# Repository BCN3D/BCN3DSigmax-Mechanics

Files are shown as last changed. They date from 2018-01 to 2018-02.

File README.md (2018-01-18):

## What’s hold in this repository?
This repository will hold all the information about the Mechanics of the BCN3D Sigmax.
As a declared Open Source organization, it's in our mission to release all the original design files to you to be able to learn, reuse and improve. Open Source not only means code, it also concerns hardware.

We’ve managed to design and manufacture the BCN3D Sigmax thanks to our previous experience in the 3D printing industry, the ideas coming from the community, our engineering background and a narrow collaboration with our suppliers. Our goal is justify the decisions we took and share the know-how we acquired so far.

We also provide the source files for those who want to check the core of the BCN3D Sigmax. You can consult both the CAD files and the technical drawings.

For a detailed explanation about the main pillars of the mechanical design of the Sigma and Sigmax, please check the repository [BCN3D Sigma - Mechanics](https://github.com/BCN3D/BCN3DSigma-Mechanics).

Regarding the Sigmax, the main objectives were:

 - Sigma and Sigmax must share as many references as possible

 - The Sigmax is targeting a more demanding customer, hence its performance and reliability must excel. 

The first goal was accomplished with a careful mechanical design, which ultimately allowed us to just modify few parts in the X and Z axis, change some wiring references and widen the aluminium frame. 

However, such big sheet metal parts, especially the frame, can be a challenge. Luckily, our previous experience in sheet metal manufacturing technologies eased the design process and the communication with our partners, so the suppliers have been able to provide high quality components since the very beginning of the production. 

The second goal has been achieved by improving the performance of certain key subassemblies. The most important change can be seen in the extruders. The Sigmax features the globally renowned Bondtech drivegears. These exceptional pieces of hardware, together with mighty stepper motors with planetary  gearbox has increased dramatically the reliability of the printer.

In addition, the Sigmax can be covered, a key feature for those intending to print large models with technical materials which may tend to warp. In order to ensure the safe operation of the printer, some heatsinks have been added in the most critical stepper motors.

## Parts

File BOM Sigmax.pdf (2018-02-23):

MANUFACTURER | CODE | PART NAME | UNITS
RiT | 14054 | A3BCN3DSigma Structure | 1
RiT | 14056 | Lower platform Sigma X | 1
RiT | 14057 | Reinforcement. Sigma X | 1
GLAS FORM S.L. | 14061 | Electronics cover Sigma X | 1
GLAS FORM S.L. | 14062 | Bottom cover Sigma X | 1
REMS | 14063 | ESPUMA TOP CC NEGRE FRESADO 750*550*85 Sigma X | 1
REMS | 14064 | ESPUMA CABEZALES CC BLANCO TROQ. 630 Sigma X | 1
MECANIZADOS CHAVES S.C.P. | 14065 | Transmission Bar Sigma X 675mm | 1
IGUS | 14073 | Cojinete de pedestal igubal®, Ø8mm KSTM-08 | 1
VIDRASA | 14066 | Placa borosilicato422x299x4mm | 1
ROBOTDIGG | 14067 | SSR25A DC-DC Solid-state Relay Sigma X | 1
ROBOTDIGG | 14045 | Motor heatsink black 28*28*15mm | 2
RUNICE | | GT2 OPEN BELT | 2
AXON' CABLE S.A.S. | 14052 | FFC Hotend 0 P567306A | 1
AXON' CABLE S.A.S. | 14053 | FFC Hotend 1 P567305A | 1
AXON' CABLE S.A.S. | 14051 | FFC Extruder 0 P567303A | 1
AXON' CABLE S.A.S. | 14050 | FFC X0 stepper P567304A | 1
CHANGZHOU SMART AUTOMATION | 14069 | Hot Bed Cable | 1
CHANGZHOU SMART AUTOMATION | 14070 | Power AC Cable | 1
CHANGZHOU SMART AUTOMATION | 14071 | Relay to mainboard Cable | 1
CHANGZHOU SMART AUTOMATION | 14072 | Power Supply to relay | 1
FLAK | 14075 | Caixa exterior cartró | 1
FLAK | | Caixa interior accesoris | 1
TAMEC | 14074 | Nozzel Offset Shim 0.05mm inox A.5 | 10
BONDTECH | 14044 | Drivegear kit 2,85/3,00 | 2
PRODUCTOS IMEDIO / bolton adhesives | 14077 | UHU STIC 21g | 1
MECANIZADOS CHAVES S.C.P. | 14049 | Extruder Body Left [X] | 1
MECANIZADOS CHAVES S.C.P. | 14048 | Extruder Tensor Left [X] | 1
MECANIZADOS CHAVES S.C.P. | 14047 | Extruder Body Right [X] | 1
MECANIZADOS CHAVES S.C.P. | 14046 | Extruder Tensor Right [X] | 1
RUNICE | 14068 | MGN9H rail 652mm Sigma X | 1
BARNES | 14082 | C0240-042-1000-M | 2
GRAMAGRAF | 14079 | Quick start guide Sigmax | 1
GRAMAGRAF | 11001 | Vinil logos | 1
ROBOTDIGG | | NEMA 17 40mm | 2
AIMAN G Z, S.L. | 10919 | Neodimio Aro 9.5-5.5-2 / NA009 | 4
KUONGSHUN ELECTRONIC | 10920 | Ball magnet 6mm diameter | 4
ALBIMAR | 10928 | Espátula 40mm / 18B305 | 1
ALBIMAR | 10934 | Tornavis estrella PH0X50 / 39D773 | 1
ALBIMAR | 10939 | Alicates 140mm C/Muelle / 32D726 | 1
ALBIMAR | 10964 | Llave Allen Pavonada 1,5mm | 1
ALBIMAR | 10965 | Llave Allen Pavonada 2,55mm | 1
ALBIMAR | 10966 | Llaven Allen Pavonada 4mm | 1
AXON' CABLE S.A.S. | 10858 | BCN3DSigma-Cable FFC X1 Motor | 1
AXON' CABLE S.A.S. | 10860 | BCN3DSigma-Cable FFC Z Motor | 1
AXON' CABLE S.A.S. | 10861 | BCN3DSigma-Cable FFC Y Motor | 1
AXON' CABLE S.A.S. | 10862 | BCN3DSigma-Cable FFC Extruder 1 | 1
BARNACORK S.L. | 10906 | Hotbed cork 297x210x3 mm corcho aglomerado | 2
REMS | 11037 | TOOL FOAM TRAY 310x210x35 scell R | 1
BRAFIM | 10976 | Conjunto protección Sigma protecció | 1
EET EUROPARTS | 10273 | Cable alimentación IEC 1,5m | 1

# BOM SIGMAX

MANUFACTURER | CODE | PART NAME | UNITS
EET EUROPARTS | 10082 | Cable USB 2.0 1,8m / CU03 | 1
CHANGZHOU SMART AUTOMATION | 10869 | BCN3DSigma-Cable LCD 0P12D | 1
CHANGZHOU SMART AUTOMATION | 10871 | BCN3DSigma-Cable Endstop Y | 1
CHANGZHOU SMART AUTOMATION | 10872 | BCN3DSigma-Cable Endstop X | 2
CHANGZHOU SMART AUTOMATION | 10873 | BCN3DSigma-Cable Endstop Z | 2
CHANGZHOU SMART AUTOMATION | 10874 | BCN3DSigma-Cable SD 0P19C | 1
CHANGZHOU SMART AUTOMATION | 10901 | SM35HT36-1004A-08A (Nema 14 36mm) | 2
CHANGZHOU SMART AUTOMATION | 10903 | SM42HT33-1334L with Tr8*2 260mm length + nut | 1
CHANGZHOU SMART AUTOMATION | 10987 | SM42HT47-1684A-37F (nema 17 42mm) | 1
ALBIMAR | 10992 | Arandelas nylon 3.2x7x0.5 | 38
ALBIMAR | 10826 | Patas para tornillo 7,1x15,9mm / 15129 | 4
ALBIMAR | 10931 | Nylon UL94 V2 6/6, RMS-01 / N-5E | 4
| 10828 | BCN3DSigma-Stepper Holder Right | 1
RiT | 10829 | BCN3DSigma-Stepper Holder Left | 1
RiT | 10830 | BCN3DSigma-X Axis Idler | 2
RiT | 10831 | BCN3DSigma-Belt Clamp | 2
RiT | 10835 | BCN3DSigma-Lower Cover | 2
RiT | 10836 | BCN3DSigma-Upper Cover | 2
RiT | 10837 | BCN3DSigma-Hotend Plate | 2
RiT | 10838 | BCN3DSigma-Y Axis Idler | 2
RiT | 10839 | BCN3DSigma-Y Idler Tensioner | 2
RiT | 10840 | BCN3DSigma-Guide Spacer | 2
RiT | 10843 | BCN3DSigma-SD Holder | 1
RiT | 10845 | BCN3DSigma-Spool Support | 4
RiT | 10846 | BCN3DSigma-X Support | 2
RiT | 10847 | BCN3DSigma-Connection plate | 2
RiT | 10849 | BCN3DSigma-Purger Base Left | 1
RiT | 10850 | BCN3DSigma-Purger Base Right | 1
RiT | 10851 | BCN3DSigma-X Plate Left | 1
RiT | 10852 | BCN3DSigma-X Plate Right | 1
RiT | 10853 | BCN3DSigma-Connection Board Support | 2
RiT | 10854 | BCN3DSigma-Y Stepper Holder | 1
RiT | 10918 | BCN3DSigma-Extruder driver cover | 2
RiT | 10956 | BCN3DSigma-X Stepper Driver Holder Left | 1
RiT | 10957 | BCN3DSigma-X Stepper Driver Holder Right | 1
RiT | 10983 | BCN3DSigma-Z Stepper Holder | 1
FERPLAST, S.L. | 10894 | BCN3DSigma-Window PET-G 2mm incoloro | 2
FLAK SL. | 11035 | tub eines | 1
GLAS FORM S.L. | 10890 | BCN3DSigma-Inner covers PS blau | 1
GLAS FORM S.L. | 10892 | BCN3DSigma-LCD cover PS blau | 1
GRAMAGRAF | 11001 | BCN3D Sigma Logo (2 logos) | 1
GRAMAGRAF | 11002 | SIGMA CE Label | 1
GRAMAGRAF | 11004 | Hot surface Label+ Warning hard injury | 2
GRAMAGRAF | 11006 | Adesivo Tuercas | 2
GRAMAGRAF | 10969 | FOLLETOS GARANTIA + quick start guide | 1
I.M.C. esquerda S.L. | 10915 | Silicone Cloth Pieza 36x13x2 mm silicona | 2
RUNICE | 10446 | Pulley GT2, 20 Teeth 5mm Bore for 6mm width belt | 2
RUNICE | 11071 | Idler pulley 20 teeth | 4
RUNICE | 10875 | MGN9H rail 360 mm | 2
JINAN YUKI | 10877 | LMF12UU Linear bearing | 2
JINAN YUKI | 10878 | SK12 Shaft Support | 4
RUNICE | 10879 | KFL08 Bearing Pillow Block | 2
RUNICE | 10883 | GT2 Pulley 20 teeth 8mm bore for 12mm width belt | 1

MANUFACTURER | CODE | PART NAME | UNITS
RUNICE | 10884 | GT2 Pulley 20 teeth 5mm bore for 12mm width belt | 1
RUNICE | 10885 | GT2 Pulley 20 teeth 8mm bore for 6mm width belt | 2
JINAN YUKI | 10886 | Ball Bearing MR105zz | 2
RUNICE | 10880 | GT2 Belt 6mm width closed belt 810mm | 2
RUNICE | 10882 | GT2 Belt 12mm width closed belt 112mm | 1
KUONGSHUN ELECTRONIC | 10897 | PTFE Teflon Tube, ID=4mm OD=6mm [m] / Q99 | 1
ULIKELED | 10945 | Led strip RGB 5050 assembled | 2
ARES | 10973 | SD Reader | 1
KUONGSHUN ELECTRONIC | 10476 | USB Cable Extension | 1
MECANIZADOS CHAVES S.C.P. | 10899 | BCN3DSigma-Y Belt tensor | 1
MECANIZADOS CHAVES S.C.P. | 10900 | BCN3DSigma-Hot block HE | 2
MECANIZADOS CHAVES S.C.P. | 10905 | BCN3D Sigma-Z Bar | 2
MECANIZADOS CHAVES S.C.P. | 10911 | BCN3DSigma-Heatbreak HE | 2
MECANIZADOS CHAVES S.C.P. | 10912 | BCN3DSigma-Heatsink HE | 2
MECANIZADOS CHAVES S.C.P. | 10986 | Idler Pulley Shaft | 4
MISCO | 10210 | SD Card 8GB | 2
MUELLES Y RESORTES BOSCH, S.L. | 10895 | Muelle 15,75xINT=5,7x1:E7 AMOLADO / M03C02.0P04Z | 3
MUELLES Y RESORTES BOSCH, S.L. | 10896 | Muelle 25,4xINT=3,96X1,1:E:14,5 AMOLADO / M07C00.0P13Z 2
ONDARADIO | 10887 | Power Supply 24V 320W / RSP-320-24 | 2
AXON' CABLE S.A.S. | 10982 | TUBE PTFE 3.18x6.35mm Natural | 2,1
DECOLETAJE 9002 | 10922 | Pneufit Coupling | 6
DECOLETAJE 9002 | 10923 | NOZZLE 0,4mm SIGMA | 2
RIERA I TUTÓ | 10841 | BCN3DSigma-Square 90 | 8
RIERA I TUTÓ | 10842 | BCN3DSigma-Square 60 | 2
RS AMIDATA | 11060 | Pantalla uLCD-35DT 4D Systems (125-7946) | 1
RS AMIDATA | 10924 | Coupling collet unión 1/4" / PI0408S (896-8333) | 14
KUONGSHUN ELECTRONIC | 10926 | SS-5-FD MICROSWITCH, 5A, PIN, SPDT, SOLDER / 682-2657 | 5
ALBIMAR | 10930 | Espaciador Redondo, Poliamida, negro 3,2x6x3 / 102-6110 | 14
RS AMIDATA | 10933 | Prensacables Adhesivos Planos / 233-190 | 11
RS AMIDATA | 10935 | Interruptor de balancín, 1881.1103 / 741-0912 | 1
RS AMIDATA | 10936 | Fusible 250V 10A 5x20mm / 541-4533 | 2
RS AMIDATA | 10938 | Cinta adhesiva Advance Tapes 205882 Blanco Mate [m] / 239-4600 1,8
RS AMIDATA | 10991 | Conector filtro IEC950 FN9260-2-06 / 188-9618 | 1
SHENZHEN XINYUJIE | 10916 | Axial fan 4010 24V 130mm PHR 2 / AV-F4020HB | 2
GICODA | 11034 | ventilador 3010 12V | 2
ARES | 11070 | Stepper Driver X axis | 2
ARES | 10907 | Stepper Driver YZE axis | 4
ARES | 10908 | Heated Bed | 2
ARES | 10909 | Mother Board | 1
ARES | 10910 | Extruder Board | 2
UTILNORM, S.L | 10888 | High Knurled Knut DIN 466 M5 / ULM 06110-05 | 2
UTILNORM, S.L | 10889 | Botón moleteado con rosca interior / 06094-004 | 4
YANCHENG XUANYUAN | 10977 | Subkit 21 (Cable Hotend) | 4
HIWIN BLOCK TECNOPOWER | 11094 | | 4

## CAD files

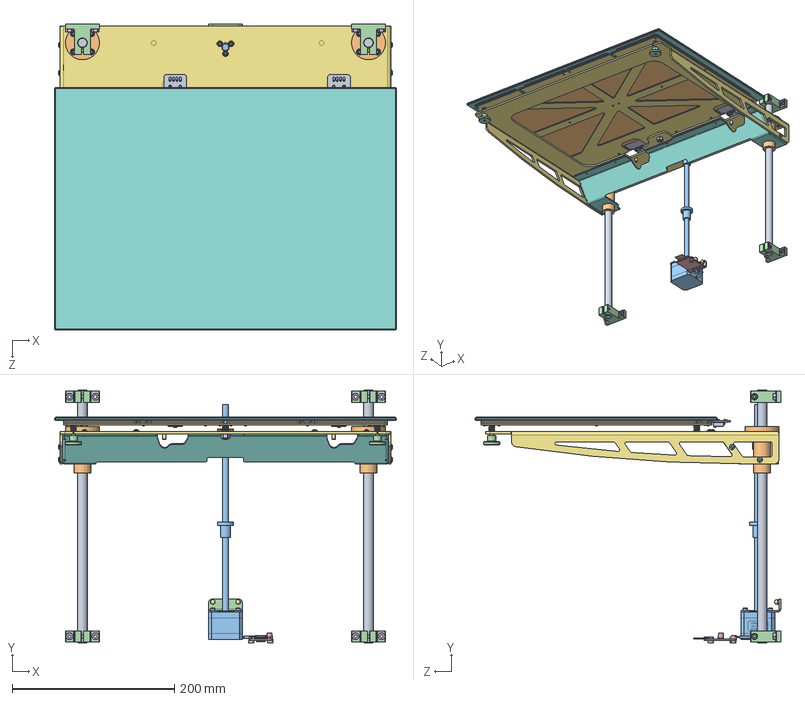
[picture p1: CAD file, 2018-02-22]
CAD/SLDPRT2016/040M03C00.0P000 Z axis.SLDASM
422.0 x 312.0 x 377.2 mm
A3DIN912 M3x6 x 8
A3DIN912 M3x8 x 3
A3DIN7981 3.2x6.5 x 9
A3DIN912 M4x12 x 4
A3DIN125 M3 x 12
A3DIN934 M5 x 8
040M03C01.0P01G Lower platform
040M03C01.0P02D Reinforcement
040M03C01.0P03B Z Bar x 2
040M03C01.0P04Z Flanged Linear Bushing x 2
040M03C01.0P05Z Z Nut
040M03C01.0P06Z Shaft Support x 4
A3DIN7991 M3x6 x 18
A3DIN985 M5
040M03C02.0P01D Upper platform
040M03C02.0P02B Glass
040M03C02.0P05E Heated bed x 2
040M03C02.0P03C Cork x 2
040M03C02.0P04Z Printing surface spring x 3
040M03C02.0P07Z Bed Thumbscrew x 2
040M03C02.0P09A Thumbscrew Label x 2
040M03C02.0P06Z Magnet x 4
A3DIN1587 M3 x 2
A3DIN912 M3x10 x 3
A3DIN934 M3 x 2
A3DIN125 M3 poliamida x 2
040M03C03.0P01Z Z Motor
040M03C03.0P02B Z Stepper Holder
040M04C00.0P03F Stepper Driver Board
040M04C00.0P06Z Ariston Spacer 3mm x 2

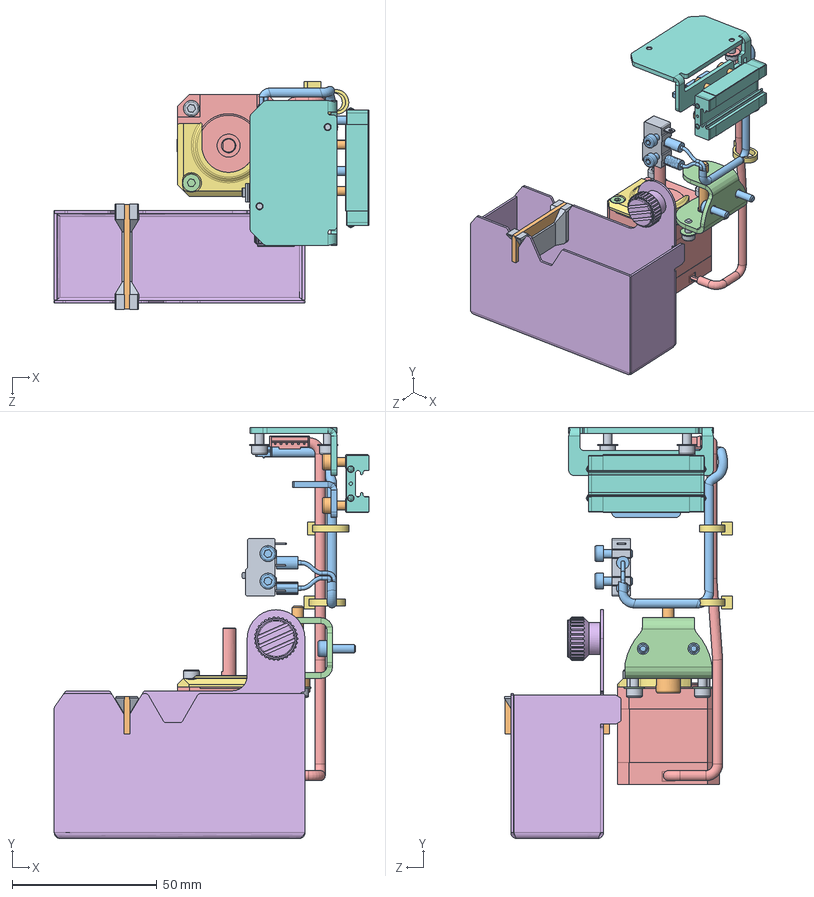
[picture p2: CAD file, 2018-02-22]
CAD/SLDPRT2016/040M05C02.0P000 X Axis Right.SLDASM
108.6 x 141.9 x 78.8 mm
A3DIN912 M3x6 x 7
A3DIN912 M3x8 x 4
A3DIN912 M3x10 x 4
A3DIN7991 M3x6
A3DIN125 M3 poliamida x 2
040M05C02.0P02C Purger Base Right
040M05C02.0P03B Stepper cover right
040M05C02.0P04B X Stepper Driver Holder Right
040M02C01.0P08Z Endstop
040M02C01.0P10A Idler pulley shaft
040M05C01.0P01D Belt Clamp
040M05C01.0P03E X Axis Idler
040M05C01.0P5Z Nema 14
040M05C01.0P08Z Purger Button
040M09C00.0P20A Zip tie x 2
040M05C00.0P02ALinear guide slide
040M05C01.0P14A Cloth Support
040M05C01.0P07A Silicone Cloth
040M09C00.0P15A Endstop X Right
A3DIN125 M3 x 2

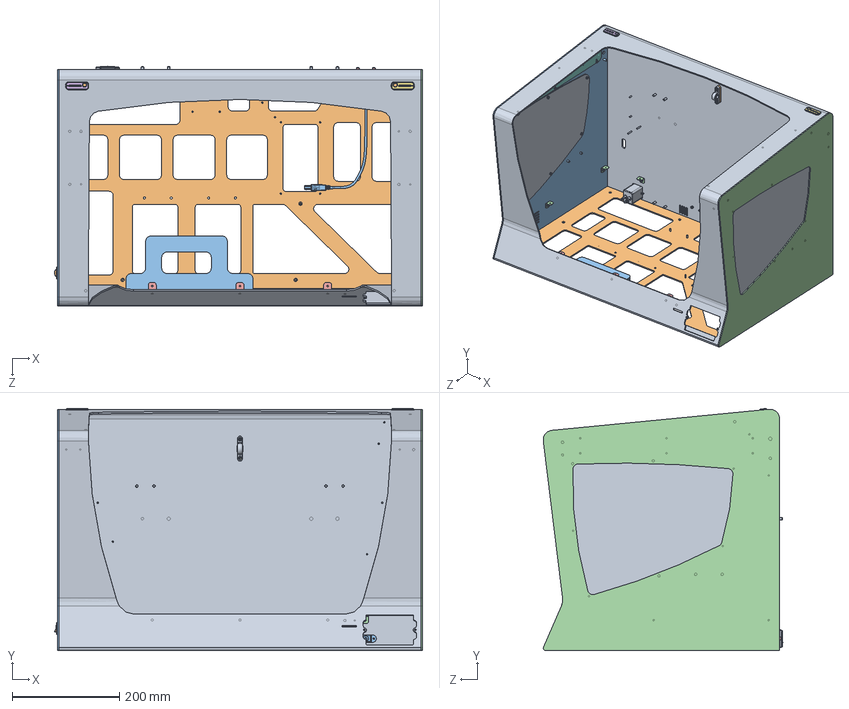
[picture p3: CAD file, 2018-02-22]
CAD/SLDPRT2016/040M01C01.0P000 Main Structure.SLDASM
686.9 x 451.8 x 447.2 mm
040M01C01.0P01G Top frame
040M01C01.0P02D Bottom frame
040M01C01.0P03C Left side
040M01C01.0P04C Right side
040M01C01.0P05C Y Idler Tensioner x 2
040M01C01.0P29F Bowden exit Left
040M01C01.0P29F Bowden exit Right
040M01C01.0P07F Guide spacer x 2
040M01C01.0P08B Window x 2
040M01C01.0P11Z Power button
040M01C01.0P12Z USB Extension Cable
040M01C01.0P15A Square 90 x 8
040M01C01.0P16A Square 60 x 3
040M01C01.0P30A Curve flat cable holder Right x 2
040M01C01.0P20C Front LED connector clamp x 2
040M01C01.0P22D Plain flat cable holder x 4
040M04C00.0P07Z Power Entry Filter
040M01C01.0P17Z Fusible
A3DIN913 M4x4 x 12
DIN7982 M3.5x13 x 2
A3DIN912 M3x10 x 2
A3DIN125 M3 poliamida x 14
A3DIN934 M3 x 48
A3DIN985 M3 x 9
040M02C01.0P14A DRY-RUNNING MOUNTED SLEEVE BRNG
040M02C01.0P15A Y Axis Pillow Bearing Spacer

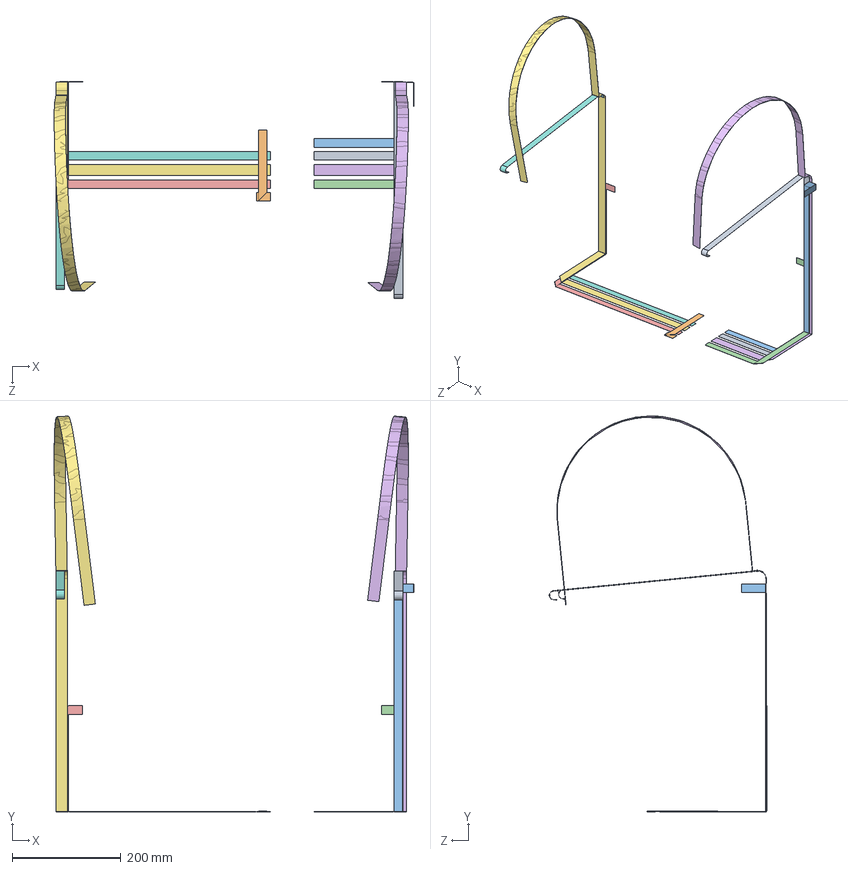
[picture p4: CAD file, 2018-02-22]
CAD/SLDPRT2016/040M09C00.0P000 Wiring.SLDASM
661.3 x 728.0 x 399.5 mm
040M09C00.0P01A FFC X1 stepper
040M09C00.0P03A FFC Z stepper
040M09C00.0P04A FFC Y stepper
040M09C00.0P05A FFC Extruder 1
040M09C00.0P06B FFC Extruder 0
040M09C00.0P08A FFC Hotend 1
040M09C00.0P07B FFC Hotend 0
040M09C00.0P02B FFC X0 stepper

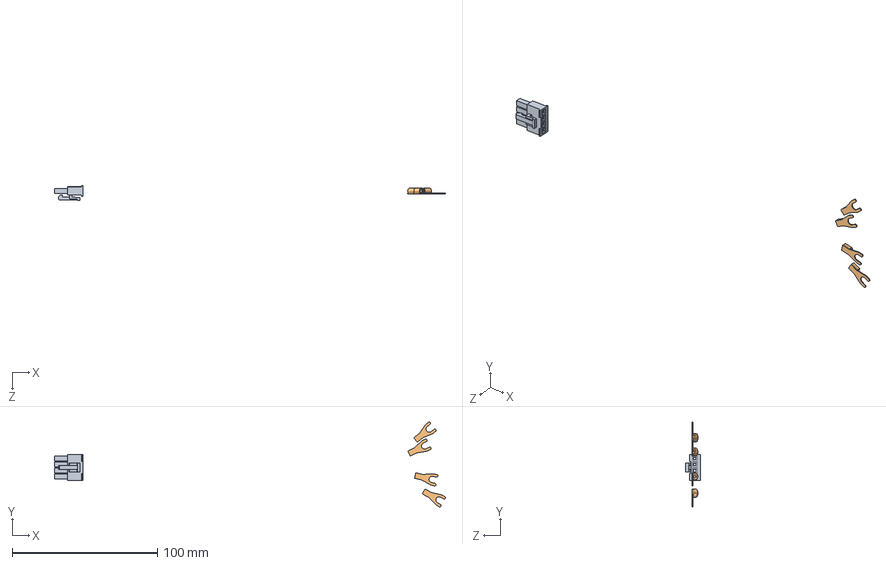
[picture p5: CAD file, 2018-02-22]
CAD/SLDPRT2016/040M09C00.0P11B Power DC cable.sldasm
268.9 x 58.3 x 10.2 mm
A3039014040
A3JST_GS42,5C x 4

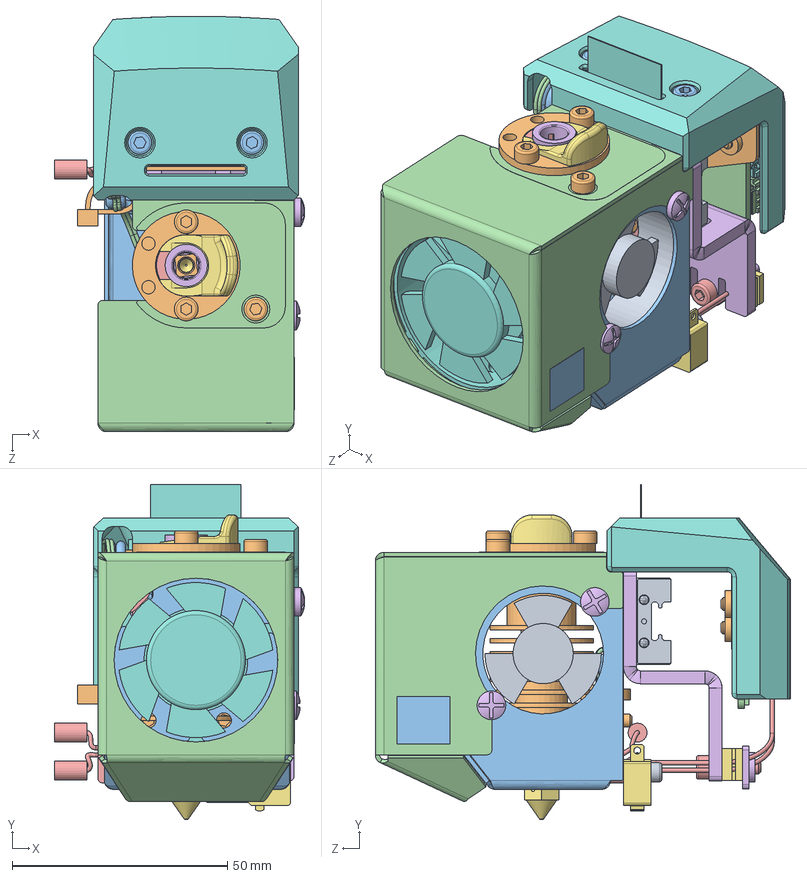
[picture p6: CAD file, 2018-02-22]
CAD/SLDPRT2016/040M06C01.0P000 Left Hotend.SLDASM
58.0 x 77.8 x 96.4 mm
A3DIN912 M2,5x10 x 2
A3DIN912 M3x6 x 9
A3DIN912 M3x8 x 4
A3DIN912 M3x18 x 3
A3DIN7991 M3x10 x 2
A3DIN7981 9.5x3.2_RationalStock x 2
A3DIN125 M3 poliamida x 4
040M06C01.0P01D Conexion cover
040M06C01.0P03Z Heat sink fan
040M06C01.0P04C Connection board support
040M06C01.0P05E Lower cover
040M06C01.0P06D Upper cover
040M06C01.0P07D Hotend Plate
040M06C01.0P08G X Plate Left
040M02C01.0P08Z Endstop
040M06C01.0P09Z Layer fan
040M06C01.0P11B Cable clip
040M06C01.0P12B Layer fan spacer
040M06C01.0P13A Flat cable clip
040M04C00.0P04B Hotend Board
040M09C00.0P16B Endstop Z Left
A3DIN913 M3x3 x 2
040M06C03.0P01C Nozzle 0.4
040M06C03.0P02C Heatbreak
040M06C03.0P03A Hot block
040M06C03.0P04G Heatsink bowden
040M06C03.1P01B Resistance 24V
040M06C03.1P02B Thermistor
040M07C01.0P04D Pneufit coupling
040M07C01.0P19Z Coupling collet
040M07C01.0P14B Coupling Clip
A3Connexio cable pla hotend
040M05C00.0P02ALinear guide slide
040M09C00.0P20A Zip tie
040M06C01.0P14A Hot surface Label
Nozzel Offset Shim 0.05mm A.5
A3DIN912 M3x12
HNKK5-3
GT2_clamp_0.1_offset - A.3

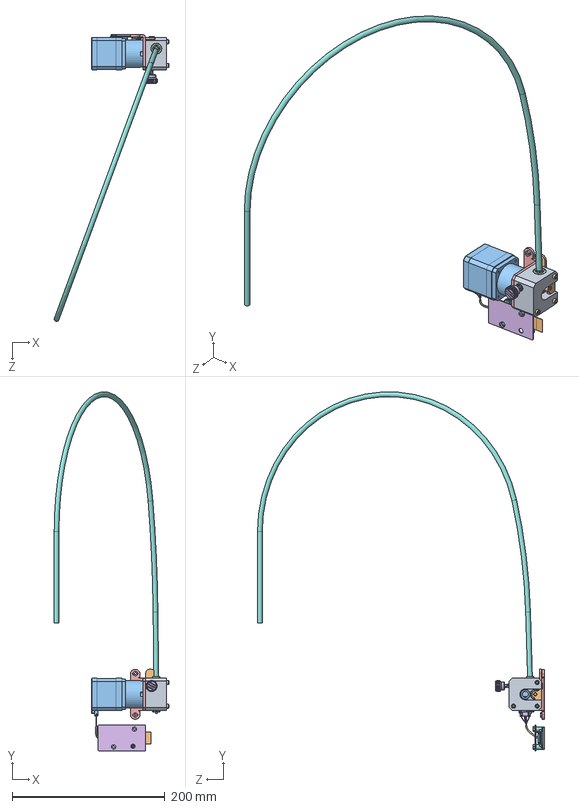
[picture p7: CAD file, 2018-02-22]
CAD/SLDPRT2016/040M07C02.0P000C Right extruder.SLDASM
150.2 x 470.4 x 376.1 mm
A3DIN934 M3 x 4
A3Connexio cable pla 15 vies
040M07C01.0P10AA Nema 17 40mm
040M07C01.0P04D Pneufit coupling x 2
040M07C01.0P05E Extruder Stepper Holder
040M07C01.0P06B Extruder driver cover
040M07C01.0P19Z Coupling collet x 2
040M04C00.0P03F Stepper Driver Board
040M07C02.0P026D Extruder Body Right
040M07C02.0P027B Extruder Tensor Right
040M07C01.0P25Z Driving Gear
040M07C01.0P24Z Driven Gear
Passador 4x24
040M05C01.0P08Z Purger Button
filament
Separador nylon negre 3.2x6x8 x 2
BCN3DSigma-M05C01.0P11C Driver spacer
A3DIN912 M3x30 x 3
040M07C01.0P13A Extruder spring
DIN931 M4x50 (91280A154)
A3DIN912 M3x8 x 3
PHR-6_PRUEBA x 2
Cable^040M07C01.0P01A Right extruder Cable
040M07C01.0P07B Bowden tube

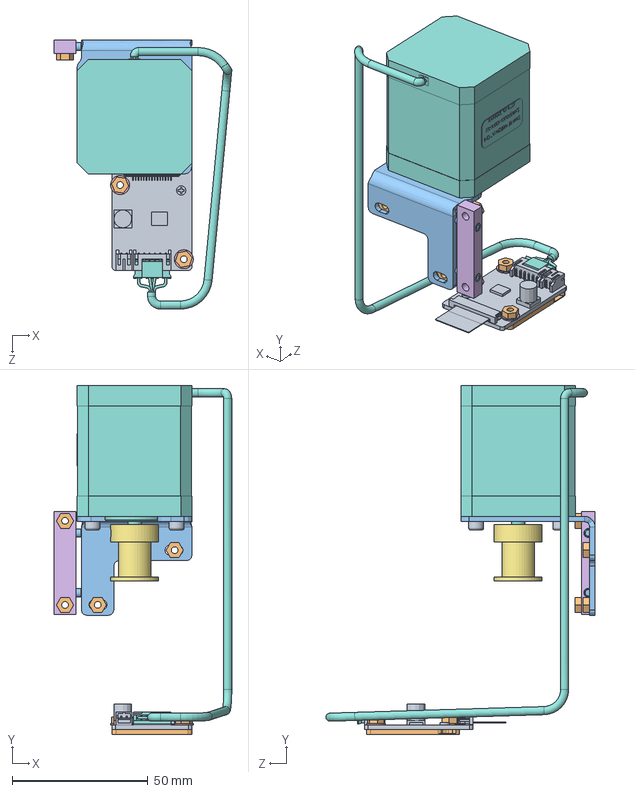
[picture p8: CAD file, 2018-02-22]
CAD/SLDPRT2016/040M02C02.0P000 Y Motor.SLDASM
65.5 x 128.6 x 99.2 mm
A3DIN912 M3x10 x 3
A3DIN934 M3 x 6
A3DIN 913 M3x10 x 2
A3DIN913 M4x3 x 2
A3DIN125 M3 poliamida x 2
040M02C02.0P02C Y Belt tensor
040M02C02.0P04Z GT2 Pulley Ø5mm Bore 12mm width
040M02C02.0P06Z Nema17 47mm
040M04C00.0P03F Stepper Driver Board
040M05C01.0P11C Driver spacer
040M02C02.0P01D Y Stepper Holder

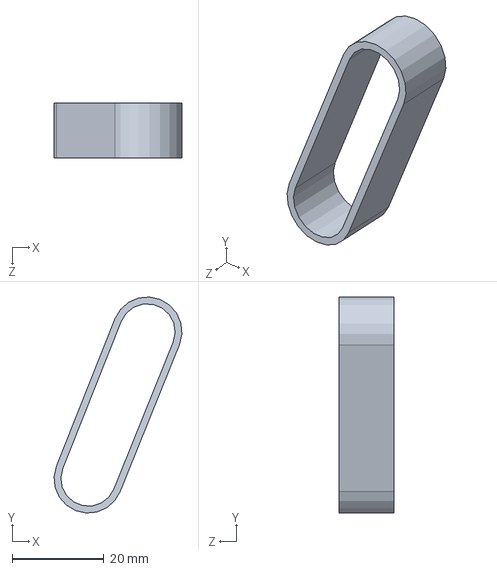
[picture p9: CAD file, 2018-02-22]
CAD/SLDPRT2016/040M02C00.0P01Z Y Main Belt.sldprt
27.9 x 47.2 x 12.0 mm

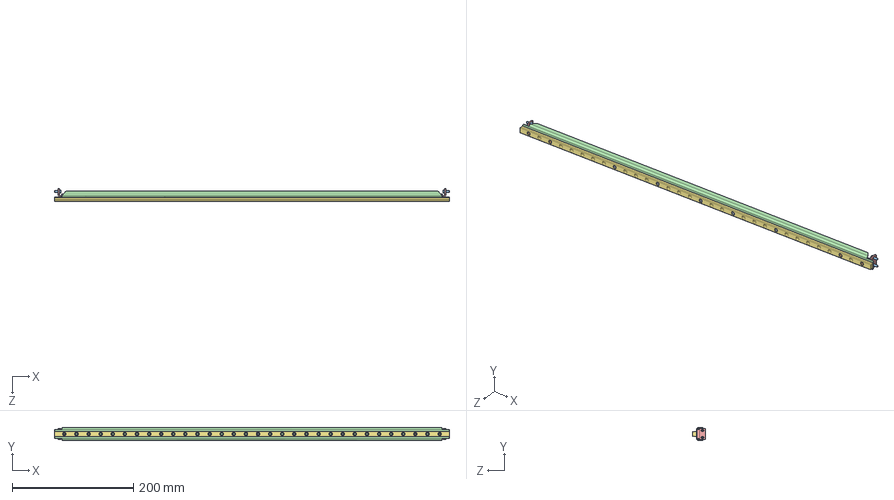
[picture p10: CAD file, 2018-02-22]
CAD/SLDPRT2016/040M05C03.0P000 X Axis Guide.SLDASM
652.7 x 21.0 x 21.5 mm
A3DIN912 M3x6 x 4
A3DIN912 M3x10 x 4
A3DIN912 M3x8 x 4
040M05C03.0P01A X Reinforcement
040M05C03.0P02D X Support x 2
040M05C03.0P03B Connection plate x 2
040M05C03.0P04Z X Guide

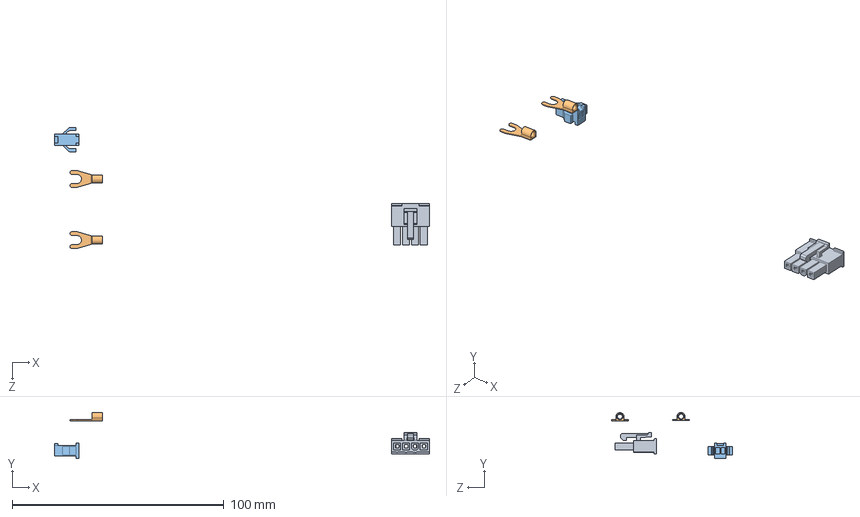
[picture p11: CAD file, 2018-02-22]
CAD/SLDPRT2016/040M09C00.0P17B Relay to mainboard cable.sldasm
177.3 x 21.8 x 57.2 mm
A3039014040
A3JST_GS42,5C x 2
SMP-02V-BC

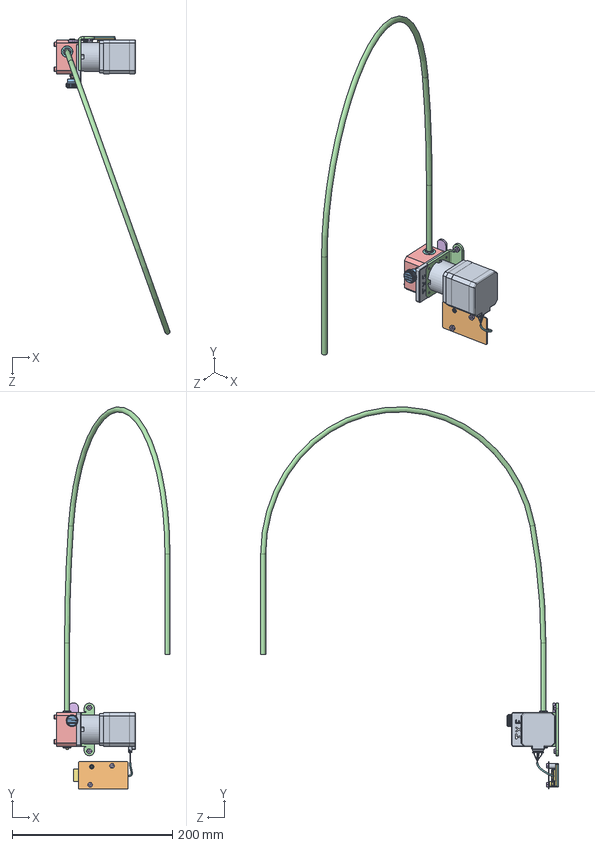
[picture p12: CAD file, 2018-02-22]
CAD/SLDPRT2016/040M07C01.0P000C Left extruder.SLDASM
144.6 x 476.2 x 371.0 mm
040M07C01.0P10AA Nema 17 40mm
040M07C01.0P25Z Driving Gear
040M07C01.0P24Z Driven Gear
040M07C01.0P05E Extruder Stepper Holder
040M07C01.0P026D Extruder Body Left
040M07C01.0P027B Extruder Tensor Left
filament
040M07C01.0P04D Pneufit coupling x 2
040M07C01.0P19Z Coupling collet x 2
Passador 4x24
040M05C01.0P08Z Purger Button
A3DIN912 M3x30 x 3
A3DIN934 M3 x 4
040M04C00.0P03F Stepper Driver Board
040M05C01.0P11C Driver spacer
Separador nylon negre 3.2x6x8 x 2
040M07C01.0P06B Extruder driver cover
040M07C01.0P13A Extruder spring
A3DIN913 M3x3
DIN931 M4x50 (91280A154)
A3DIN912 M3x8 x 3
PHR-6_PRUEBA x 2
Cable^040M07C01.0P29A Left extruder Cable

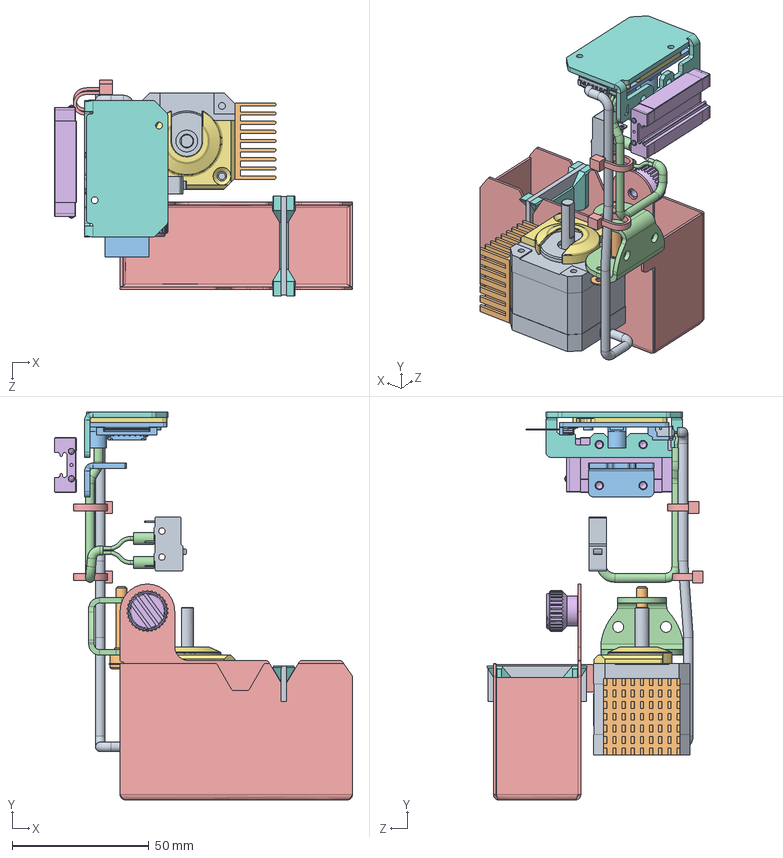
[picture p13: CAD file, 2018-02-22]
CAD/SLDPRT2016/040M05C01.0P000 X Axis Left.SLDASM
109.0 x 141.9 x 78.8 mm
040M05C01.0P5Z Nema 14
28x28x15
040M05C01.0P01D Belt Clamp
040M05C01.0P03E X Axis Idler
040M05C01.0P06C Purger Base Left
040M05C01.0P08Z Purger Button
040M05C01.0P11C Driver spacer
040M05C01.0P12B X Stepper Driver Holder Left
040M02C01.0P08Z Endstop
040M02C01.0P10A Idler pulley shaft
040M04C00.0P03F Stepper Driver Board
040M09C00.0P15A Endstop X Left
040M09C00.0P20A Zip tie x 2
040M05C00.0P02ALinear guide slide
040M05C01.0P04B Stepper cover left
040M05C01.0P14A Cloth Support
040M05C01.0P07A Silicone Cloth
A3DIN125 M3 x 2

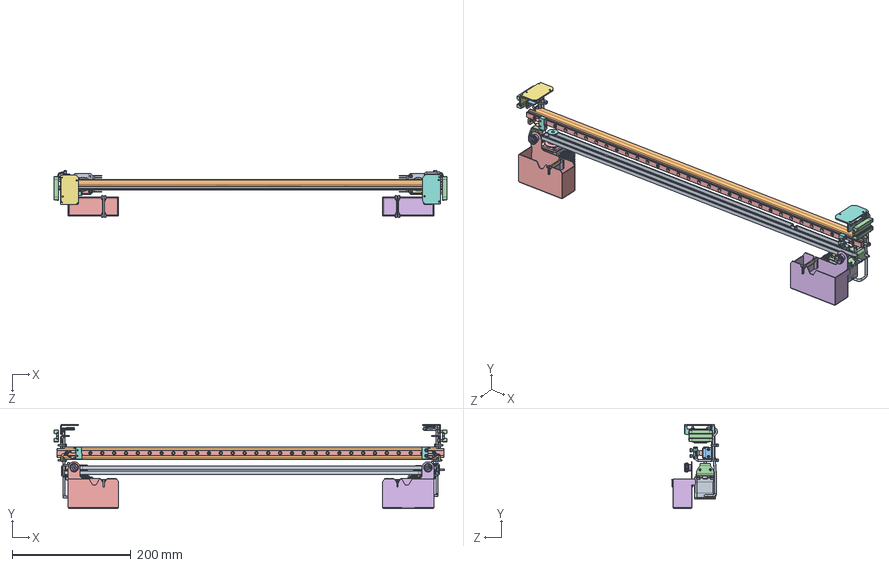
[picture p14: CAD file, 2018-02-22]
CAD/SLDPRT2016/040M05C00.0P000 X Axis.SLDASM
662.9 x 141.9 x 78.8 mm
040M05C01.0P5Z Nema 14 x 2
28x28x15 x 2
040M05C01.0P01D Belt Clamp x 2
040M05C01.0P03E X Axis Idler x 2
040M05C01.0P06C Purger Base Left
040M05C01.0P08Z Purger Button x 2
040M05C01.0P12B X Stepper Driver Holder Left
040M02C01.0P08Z Endstop x 2
040M02C01.0P10A Idler pulley shaft x 2
040M09C00.0P15A Endstop X Left
040M09C00.0P20A Zip tie x 4
040M05C00.0P02ALinear guide slide x 2
040M05C01.0P04B Stepper cover left
040M05C01.0P14A Cloth Support x 2
040M05C01.0P07A Silicone Cloth x 2
A3DIN125 M3 x 4
A3DIN912 M3x6 x 11
A3DIN912 M3x8 x 8
A3DIN912 M3x10 x 8
A3DIN7991 M3x6
A3DIN125 M3 poliamida x 2
040M05C02.0P02C Purger Base Right
040M05C02.0P03B Stepper cover right
040M05C02.0P04B X Stepper Driver Holder Right
040M09C00.0P15A Endstop X Right
040M05C03.0P01A X Reinforcement
040M05C03.0P02D X Support x 2
040M05C03.0P03B Connection plate x 2
040M05C03.0P04Z X Guide
040M02C01.0P15Z GT2 Pulley Ø4 Bearing Bore 6 Runice x 2
040M02C01.0P016Z Spacer 4x8x6 Essentra x 2
040M05C01.0P15Z GT2 Pulley Ø5 Bore 6 Runice x 2
040M05C00.0P01Z X Belt x 2

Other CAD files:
CAD/SLDPRT2016/040M06C03.0P000 Hotend.SLDASM
CAD/SLDPRT2016/040M07C03.0P000 Bifurcation.sldasm
CAD/SLDPRT2016/040M01C03.0P000 Bottom cover.SLDASM
CAD/SLDPRT2016/040M07C02.0P000B Right extruder.SLDASM
CAD/SLDPRT2016/040M01C00.0P000 Structure.SLDASM
CAD/SLDPRT2016/040M01C01.0P02D Bottom frame.SLDPRT
CAD/SLDPRT2016/040M01C01.0P03C Left side.SLDPRT
CAD/SLDPRT2016/040M01C01.0P04C Right side.SLDPRT
CAD/SLDPRT2016/040M01C01.0P05C Y Idler Tensioner.SLDPRT
CAD/SLDPRT2016/040M01C01.0P07F Guide spacer.SLDPRT
CAD/SLDPRT2016/040M01C01.0P08B Window.SLDPRT
CAD/SLDPRT2016/040M01C01.0P11Z Power button.SLDPRT
CAD/SLDPRT2016/040M01C01.0P12Z USB Extension Cable.SLDPRT
CAD/SLDPRT2016/040M01C01.0P15A Square 90.SLDPRT
CAD/SLDPRT2016/040M01C01.0P16A Square 60.SLDPRT
CAD/SLDPRT2016/040M01C01.0P17Z Fusible.SLDPRT
CAD/SLDPRT2016/040M01C01.0P20C Front LED connector clamp.SLDPRT
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

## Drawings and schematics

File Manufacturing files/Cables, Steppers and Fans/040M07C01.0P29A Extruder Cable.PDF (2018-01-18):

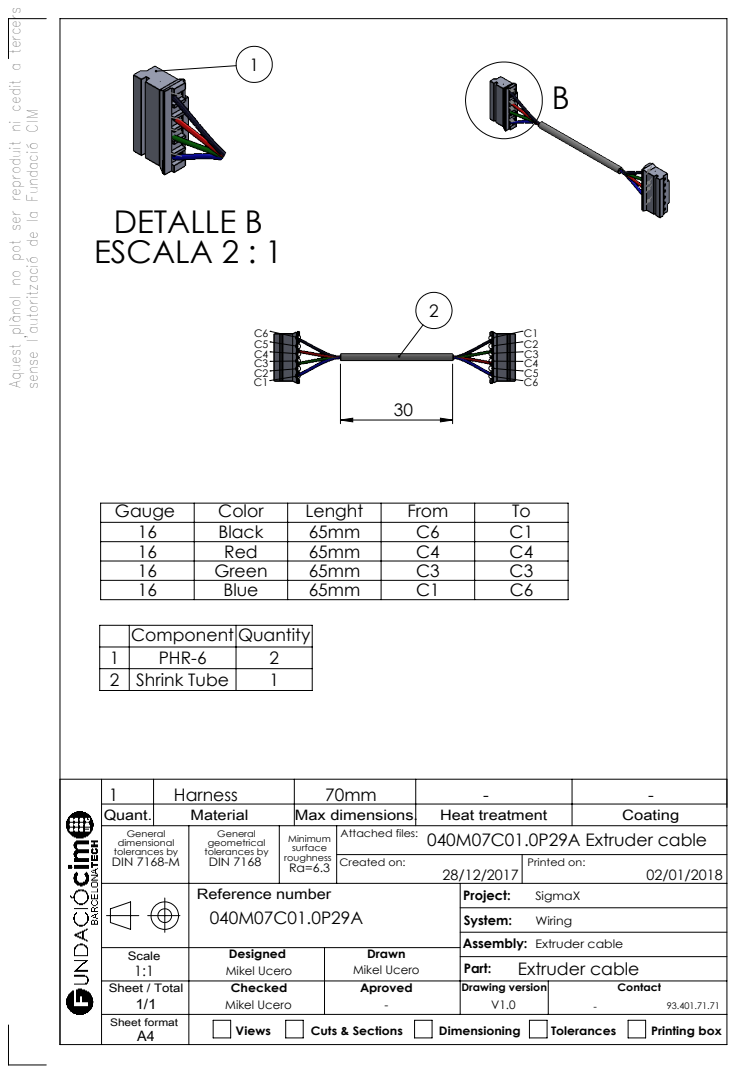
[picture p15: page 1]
Max dimensions.; Heat treatment; Coating; Created on:; Printed on:; Views; Cuts & Sections; Dimensioning; Tolerances; Printing box; DETALLE B; Extruder cable

Aquest plànol no pot ser reproduit ni cedit a tercers
ESCALA 2 : 11

sense l'autorització de la Fundació CIM

Gauge | Color | Lenght | From | To
16 | Black | 65mm | C6 | C1
16 | Red | 65mm | C4 | C4
16 | Green | 65mm | C3 | C3
16 | Blue | 65mm | C1 | C6
Component Quantity
1 | PHR-6 | 2
2 | Shrink Tube | 1

General dimensional tolerances by DIN 7168-M | General geometrical tolerances by DIN 7168 | Minimum surface roughness Ra=6.3 | Attached files: 040M07C01.0P29A Extruder cable

Reference number 040M07C01.0P29A | Project: SigmaX System: Wiring Assembly: Extruder cable

Scale 1:1 | Designed Mikel Ucero | Drawn Mikel Ucero

Sheet / Total 1/1 | Checked Mikel Ucero | Aproved - V1.0 | Drawing version | Contact -93.401.71.71

Sheet format A4

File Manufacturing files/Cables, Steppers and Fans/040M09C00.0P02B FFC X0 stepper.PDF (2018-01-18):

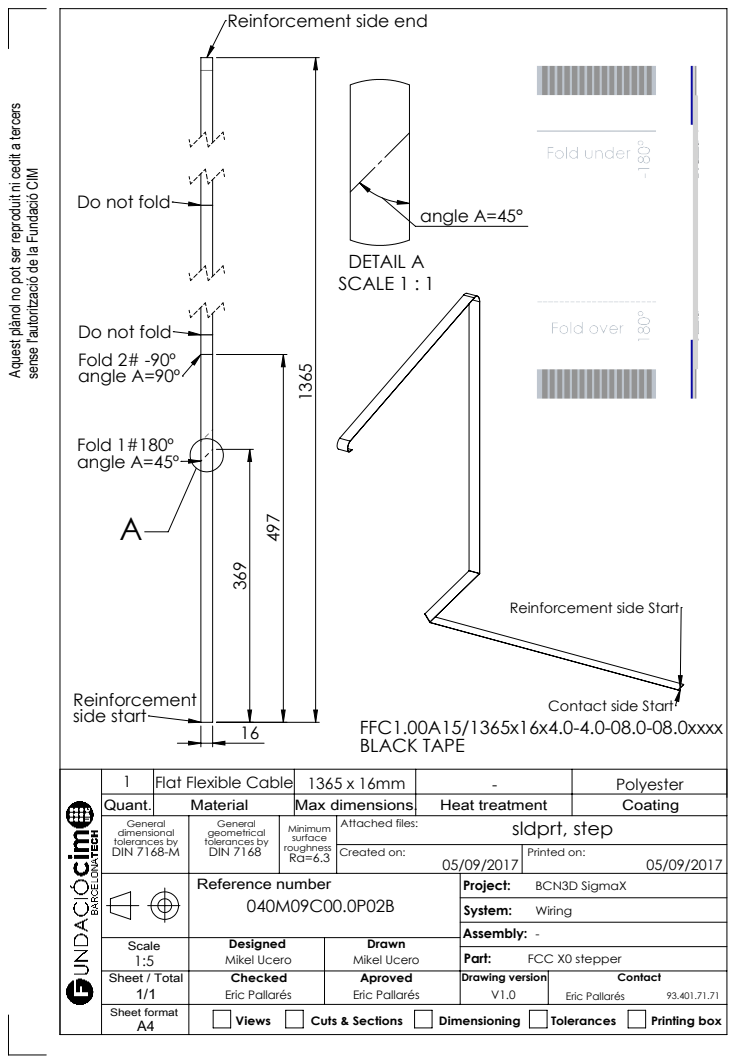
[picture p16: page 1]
Max dimensions.; Heat treatment; Coating; Created on:; Printed on:; Views; Cuts & Sections; Dimensioning; Tolerances; Printing box; FCC X0 stepper; Polyester; Fold 1#180º angle A=45º; side start; BLACK TAPE; angle A=45°; DETAIL A SCALE 1 : 1

Reinforcement side end

Aquest plànol no pot ser reproduit ni cedit a tercers

sense l'autorització de la Fundació CIM
Do not fold

Fold 2# -90º
angle A=90º

Reinforcement side Start

Contact side Start

Flat Flexible Cable
Quant.

General dimensional tolerances by DIN 7168-M | General geometrical tolerances by DIN 7168 | Minimum surface roughness Ra=6.3 | Attached files: sldprt, step

Reference number 040M09C00.0P02B | Project: BCN3D SigmaX System: Wiring Assembly: -

Scale 1:5 | Designed Mikel Ucero | Drawn Mikel Ucero

Sheet / Total 1/1 | Checked Eric Pallarés | Aproved Eric Pallarés | Drawing version V1.0 | Contact Eric Pallarés 93.401.71.71

Sheet format A4

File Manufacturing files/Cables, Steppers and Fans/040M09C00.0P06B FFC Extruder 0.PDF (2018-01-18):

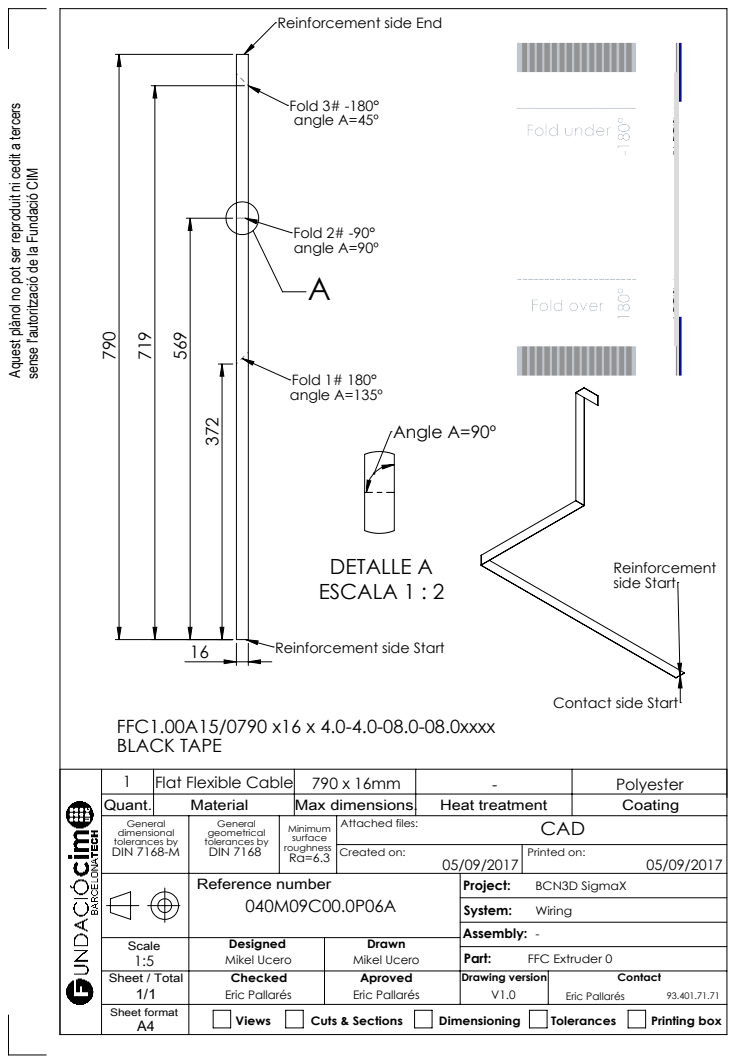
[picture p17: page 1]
Max dimensions.; Heat treatment; Coating; Created on:; Printed on:; Views; Cuts & Sections; Dimensioning; Tolerances; Printing box; FFC Extruder 0; Polyester; Fold 3# -180° angle A=45º; Fold 2# -90° angle A=90º; Fold 1# 180° angle A=135º; side Start; DETALLE A ESCALA 1 : 2; Angle A=90º

Reinforcement side End

Aquest plànol no pot ser reproduit ni cedit a tercers

sense l'autorització de la Fundació CIM

Reinforcement side Start

Contact side Start

FFC1.00A15/0790 x16 x 4.0-4.0-08.0-08.0xxxx
BLACK TAPE
Flat Flexible Cable
Quant.

General dimensional tolerances by DIN 7168-M | General geometrical tolerances by DIN 7168 | Minimum surface roughness Ra=6.3 | Attached files: | CAD

Reference number 040M09C00.0P06A | Project: BCN3D SigmaX System: Wiring Assembly: -

Scale 1:5 | Designed Mikel Ucero | Drawn Mikel Ucero

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

Sheet format A4

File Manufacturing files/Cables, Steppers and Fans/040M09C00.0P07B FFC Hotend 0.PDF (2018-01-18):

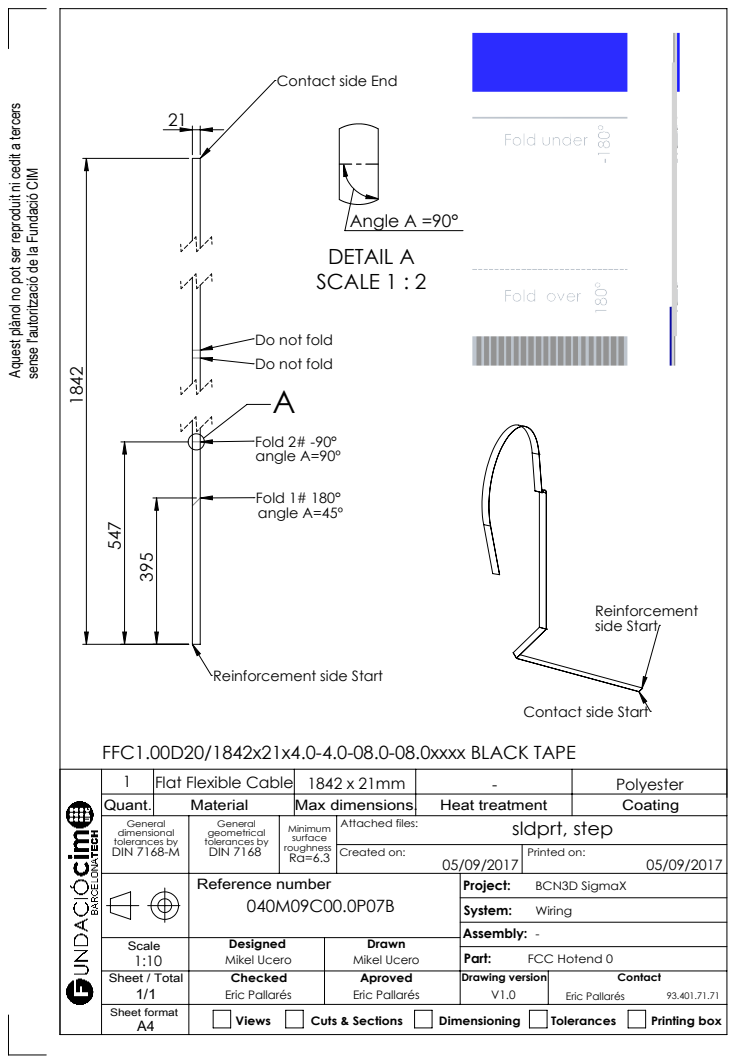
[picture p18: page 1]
Max dimensions.; Heat treatment; Coating; Created on:; Printed on:; Views; Cuts & Sections; Dimensioning; Tolerances; Printing box; FCC Hotend 0; Polyester 395; Fold 2# -90° angle A=90º; Fold 1# 180° angle A=45º; side Start; Angle A =90° DETAIL A SCALE 1 : 2

Contact side End

Aquest plànol no pot ser reproduit ni cedit a tercers

sense l'autorització de la Fundació CIM

Do not fold

Reinforcement side Start

Contact side Start

FFC1.00D20/1842x21x4.0-4.0-08.0-08.0xxxx BLACK TAPE
Flat Flexible Cable
Quant.

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

Reference number 040M09C00.0P07B | Project: BCN3D SigmaX System: Wiring Assembly: -

Scale 1:10 | Designed Mikel Ucero | Drawn Mikel Ucero

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

Sheet format A4

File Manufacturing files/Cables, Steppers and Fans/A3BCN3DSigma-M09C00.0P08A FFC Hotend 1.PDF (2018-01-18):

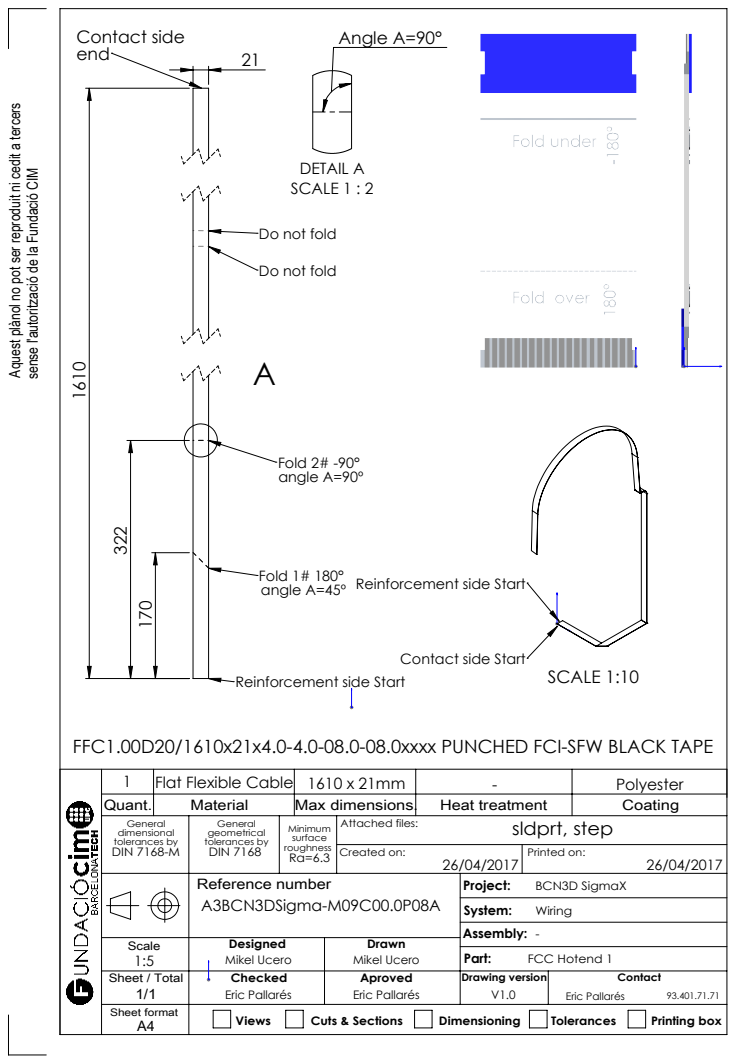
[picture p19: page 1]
Max dimensions.; Heat treatment; Coating; Created on:; Printed on:; Views; Cuts & Sections; Dimensioning; Tolerances; Printing box; Mikel Ucero; FCC Hotend 1; Polyester; Fold 2# -90° angle A=90º; Fold 1# 180° angle A=45º; Contact side; SCALE 1:10; Angle A=90°; DETAIL A SCALE 1 : 2

Aquest plànol no pot ser reproduit ni cedit a tercers

sense l'autorització de la Fundació CIM

Do not fold

Reinforcement side Start

Contact side Start

FFC1.00D20/1610x21x4.0-4.0-08.0-08.0xxxx PUNCHED FCI-SFW BLACK TAPE
Flat Flexible Cable
Quant.

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

Reference number A3BCN3DSigma-M09C00.0P08A | Project: BCN3D SigmaX System: Wiring Assembly: -

Scale 1:5 | Designed | Drawn Mikel Ucero

Sheet / Total 1/1 | Eric Pallarés | Eric Pallarés | Drawing version V1.0 | Eric Pallarés 93.401.71.71

Sheet format A4

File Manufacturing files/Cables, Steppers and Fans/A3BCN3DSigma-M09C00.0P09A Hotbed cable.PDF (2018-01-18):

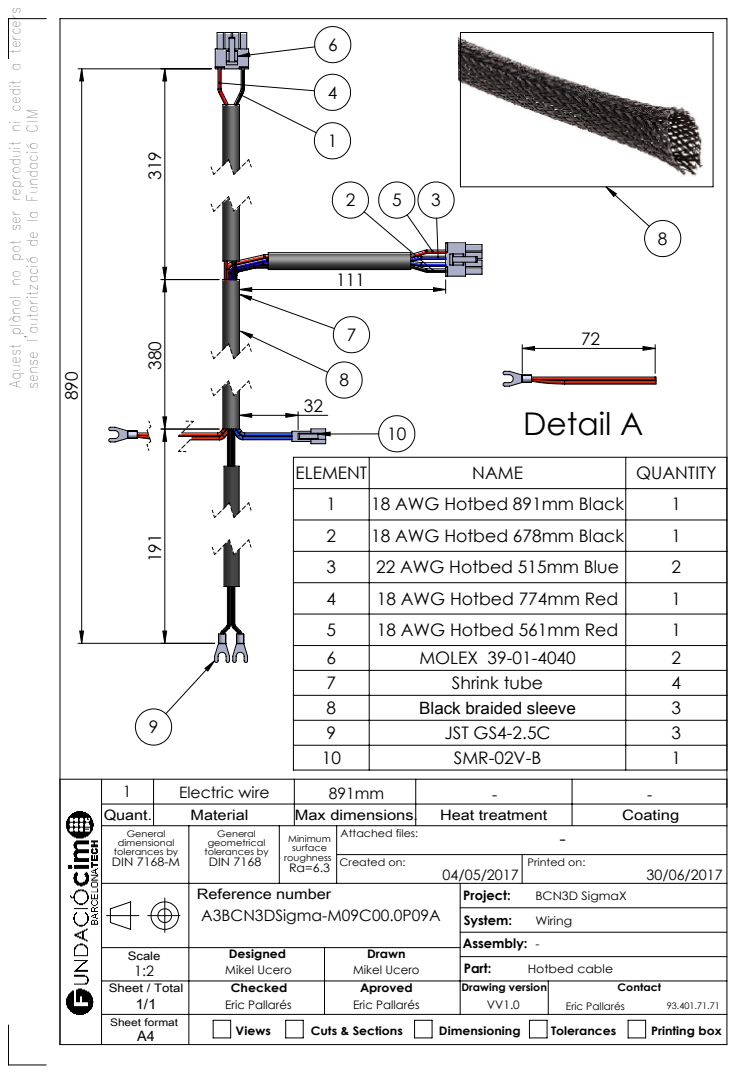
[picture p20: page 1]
Max dimensions.; Heat treatment; Coating; Created on:; Printed on:; Views; Cuts & Sections; Dimensioning; Tolerances; Printing box; Electric wire; Hotbed cable; Detail A; ELEMENT; NAME; QUANTITY 1; 18 AWG Hotbed 891mm Black; 18 AWG Hotbed 678mm Black; 22 AWG Hotbed 515mm Blue; 18 AWG Hotbed 774mm Red; 18 AWG Hotbed 561mm Red; MOLEX 39-01-4040; Shrink tube; Black braided sleeve; JST GS4-2.5C

Aquest plànol no pot ser reproduit ni cedit a tercers

sense l'autorització de la Fundació CIM

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

Reference number A3BCN3DSigma-M09C00.0P09A | Project: BCN3D SigmaX System: Wiring -Assembly:

Scale 1:2 | Designed Mikel Ucero | Drawn Mikel Ucero

Sheet / Total 1/1 | Checked Eric Pallarés | Aproved Eric Pallarés | Drawing version VV1.0 | Contact Eric Pallarés 93.401.71.71

Sheet format A4

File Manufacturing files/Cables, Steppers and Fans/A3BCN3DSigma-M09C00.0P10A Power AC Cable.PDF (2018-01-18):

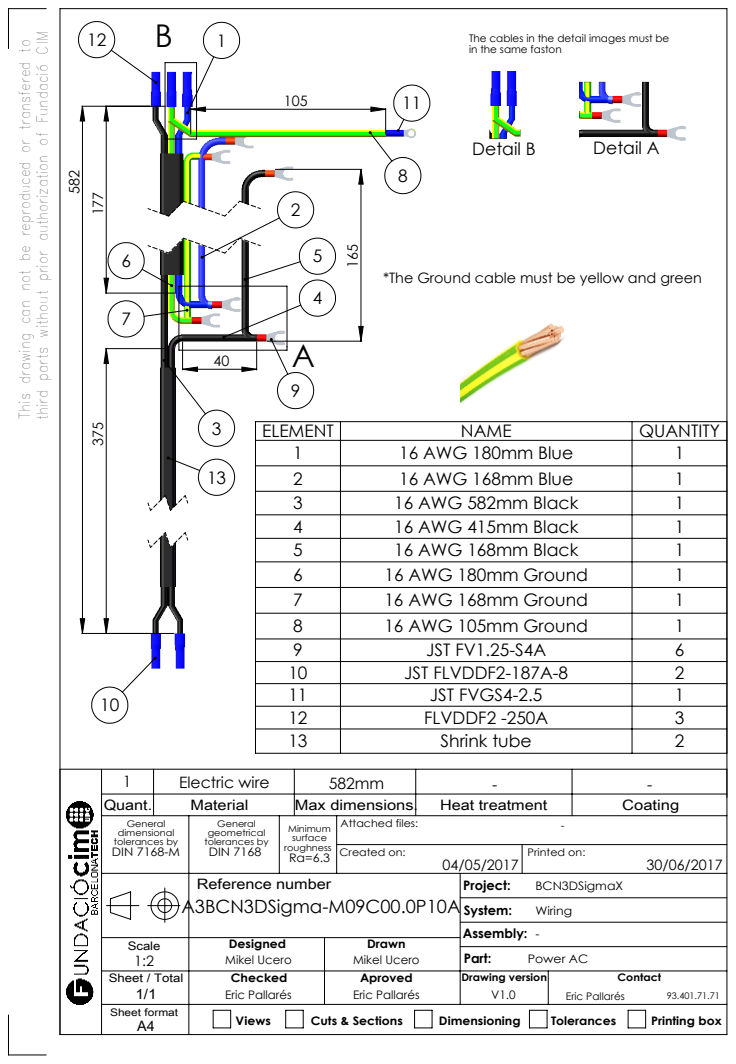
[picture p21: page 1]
Max dimensions.; Heat treatment; Coating; Created on:; Printed on:; Views; Cuts & Sections; Dimensioning; Tolerances; Printing box; Electric wire; Power AC; Detail B; Detail A; ELEMENT; NAME; QUANTITY 1; 16 AWG 180mm Blue; 16 AWG 168mm Blue; 16 AWG 582mm Black; 16 AWG 415mm Black; 16 AWG 168mm Black; 16 AWG 180mm Ground; 16 AWG 168mm Ground; 16 AWG 105mm Ground; JST FV1.25-S4A

third parts without prior authorization of Fundació CIM

The cables in the detail images must be
in the same faston

This drawing can not be reproduced or transfered to

*The Ground cable must be yellow and green

10 | JST FLVDDF2-187A-8 | 2
11 | JST FVGS4-2.5 | 1
12 | FLVDDF2 -250A | 3
13 | Shrink tube | 2

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

Reference number | Project: BCN3DSigmaX System: Wiring -Assembly:

Scale 1:2 | Designed Mikel Ucero | Drawn Mikel Ucero

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

Sheet format A4

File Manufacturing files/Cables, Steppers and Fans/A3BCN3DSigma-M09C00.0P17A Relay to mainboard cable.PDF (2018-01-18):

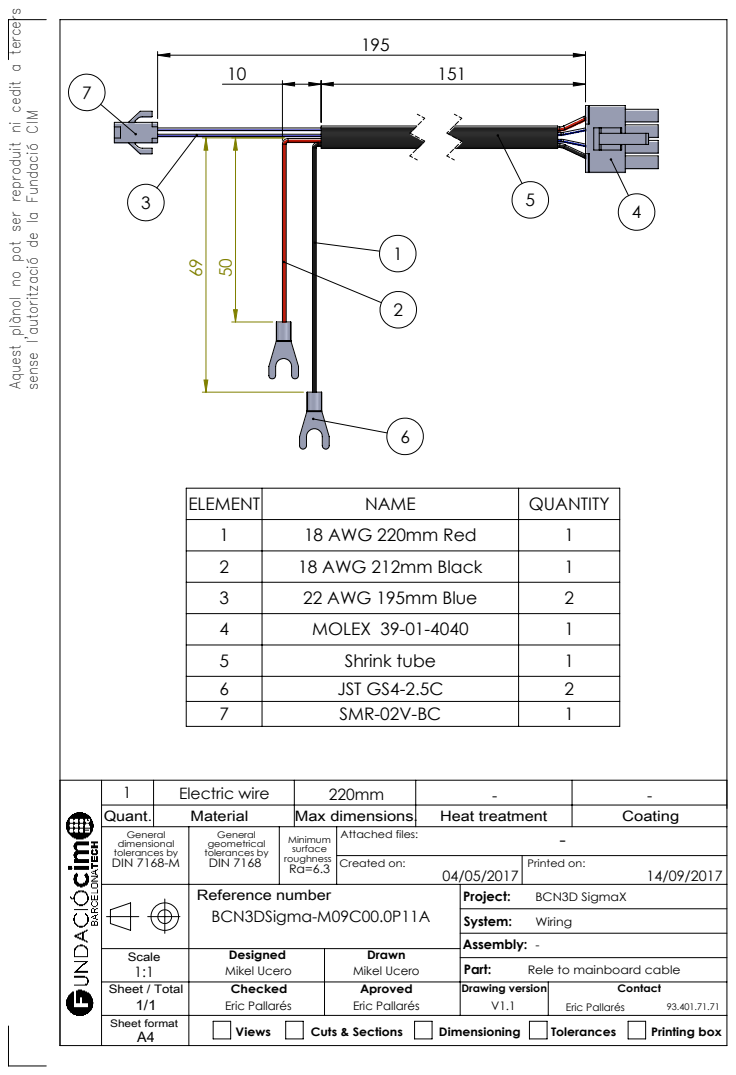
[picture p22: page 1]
Max dimensions.; Heat treatment; Coating; Created on:; Printed on:; Views; Cuts & Sections; Dimensioning; Tolerances; Printing box; Electric wire; ELEMENT; NAME; QUANTITY 1; 18 AWG 220mm Red; 18 AWG 212mm Black; 22 AWG 195mm Blue; MOLEX 39-01-4040; Shrink tube; JST GS4-2.5C; SMR-02V-BC

Aquest plànol no pot ser reproduit ni cedit a tercers

sense l'autorització de la Fundació CIM

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

Reference number BCN3DSigma-M09C00.0P11A | Project: BCN3D SigmaX System: Wiring -Assembly:

Scale 1:1 | Designed Mikel Ucero | Drawn Mikel Ucero

Rele to mainboard cable

Sheet / Total 1/1 | Checked Eric Pallarés | Aproved Eric Pallarés | Drawing version V1.1 | Contact Eric Pallarés 93.401.71.71

Sheet format A4

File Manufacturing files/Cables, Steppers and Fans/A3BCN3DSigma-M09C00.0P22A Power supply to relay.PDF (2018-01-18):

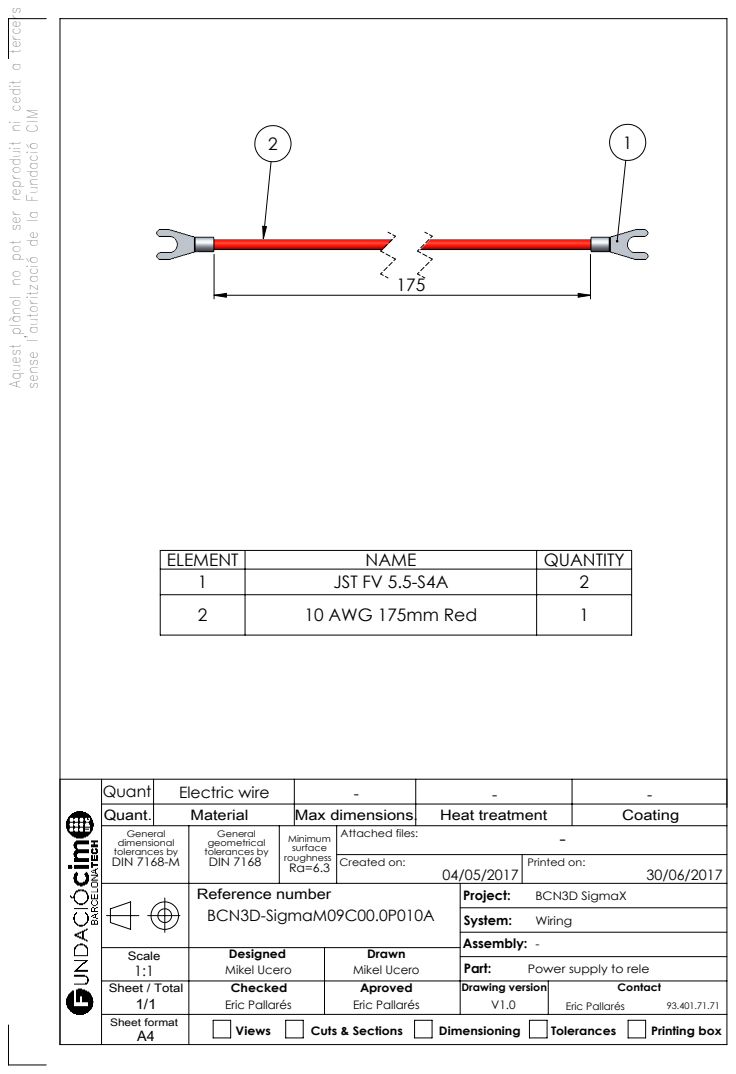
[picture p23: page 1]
Max dimensions.; Heat treatment; Coating; Created on:; Printed on:; Views; Cuts & Sections; Dimensioning; Tolerances; Printing box; Electric wire; ELEMENT; NAME; QUANTITY 1; JST FV 5.5-S4A; 10 AWG 175mm Red

Aquest plànol no pot ser reproduit ni cedit a tercers

sense l'autorització de la Fundació CIM

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

Reference number BCN3D-SigmaM09C00.0P010A | Project: BCN3D SigmaX System: Wiring -Assembly:

Scale 1:1 | Designed Mikel Ucero | Drawn Mikel Ucero

Power supply to rele

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

Sheet format A4

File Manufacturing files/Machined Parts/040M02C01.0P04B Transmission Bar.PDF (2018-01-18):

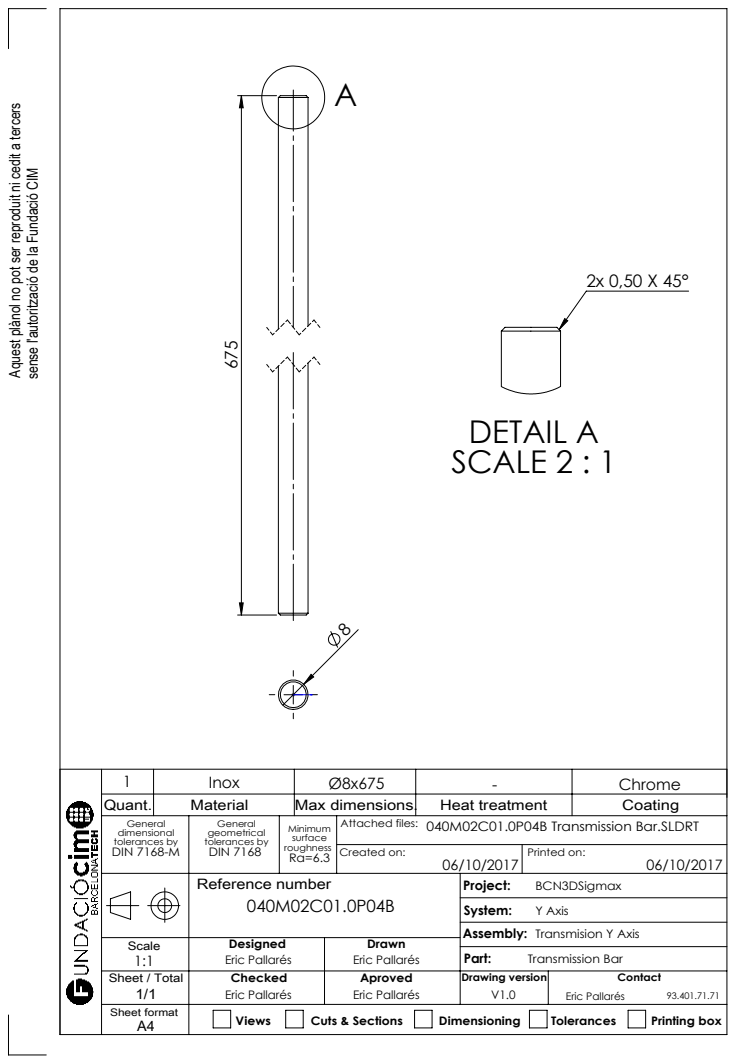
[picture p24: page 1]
Max dimensions.; Heat treatment; Coating; Created on:; Printed on:; Views; Cuts & Sections; Dimensioning; Tolerances; Printing box; Transmission Bar; Chrome 675; DETAIL A SCALE 2 : 1

Aquest plànol no pot ser reproduit ni cedit a tercers

sense l'autorització de la Fundació CIM

General dimensional tolerances by DIN 7168-M | General geometrical tolerances by DIN 7168 | Minimum surface roughness Ra=6.3 | Attached files: 040M02C01.0P04B Transmission Bar.SLDRT

Reference number 040M02C01.0P04B | Project: BCN3DSigmax System: Y Axis Assembly: Transmision Y Axis

Scale 1:1 | Designed Eric Pallarés | Drawn Eric Pallarés

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

Sheet format A4

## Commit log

2018-01-18 Sigmax CAD
    [040M01C00.0P000 Structure.SLDASM, 040M01C01.0P000 Main Structure.SLDASM, 040M01C01.0P02D Bottom frame.SLDPRT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]
2018-02-22 Add files via upload
    Added missing files
    [BCN3DSigma-M05C01.0P02G Stepper Holder Left.SLDPRT, BCN3DSigma-M05C02.0P01G Stepper Holder Right.SLDPRT]
2018-02-22 Structure fix
    [040M01C00.0P000 Structure.SLDASM, 040M01C01.0P000 Main Structure.SLDASM, 040M01C01.0P02D Bottom frame.SLDPRT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]
